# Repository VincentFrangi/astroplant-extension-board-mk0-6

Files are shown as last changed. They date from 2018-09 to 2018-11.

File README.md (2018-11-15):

# Astroplant Extension Board MK0.6

## About This Project

[Interactive BOM](http://htmlpreview.github.io/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)

## Renderings

### Top
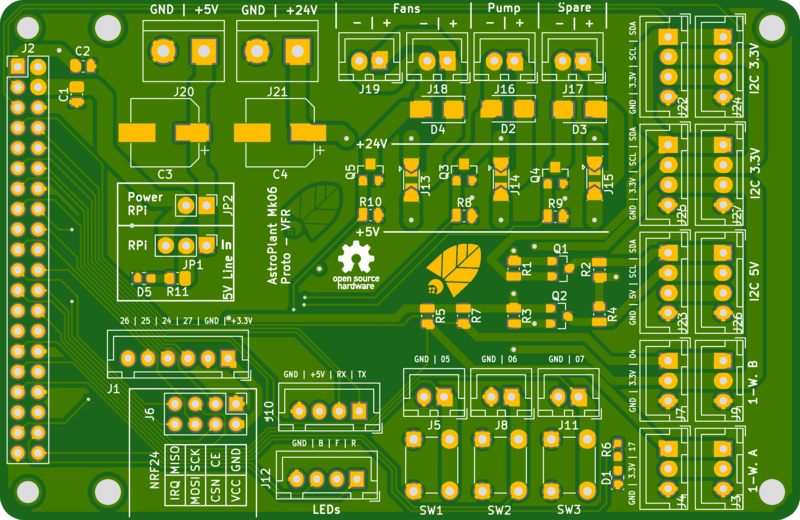
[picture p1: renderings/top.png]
Top Rendering (https://aisler.net/p/DBKSBTQF)


### Bottom
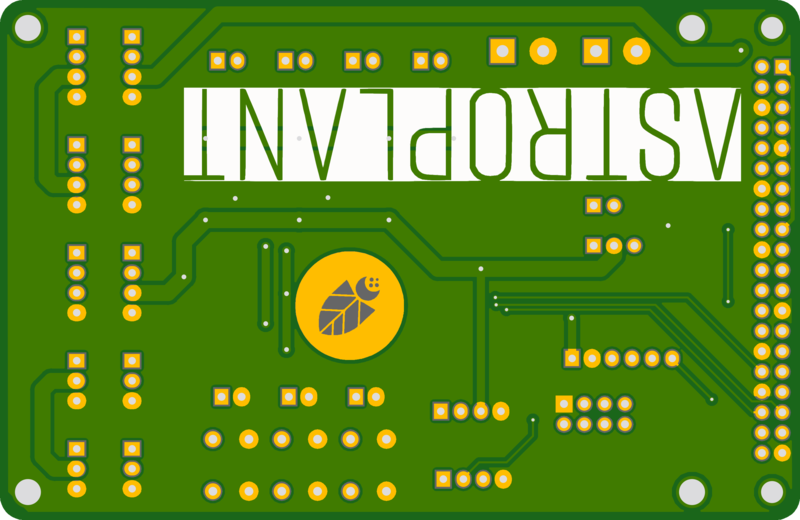
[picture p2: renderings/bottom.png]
Bottom Rendering (https://aisler.net/p/DBKSBTQF)


## BOM

|Count|Component|Details|Datasheet|
|-|-|-|-|
|2x|C1 / C2|CAP CER 0.1UF 25V X7R 0805|[Link](http://datasheets.avx.com/X7RDielectric.pdf)|
|1x|C4|CAP ALUM POLY 470UF 20% 25V SMD|[Link](https://industrial.panasonic.com/cdbs/www-data/pdf/RDD0000/ABA0000C1229.pdf)|
|1x|C3|CAP ALUM POLY 470UF 20% 6.3V SMD|[Link](https://katalog.we-online.de/pbs/datasheet/875115150005.pdf)|
|1x|D1|LED BLUE ESS II SMD|[Link](https://industrial.panasonic.com/content/data/SC/ds/ds4/LNJ937W8CRA_E.pdf)|
|3x|D2 / D3 / D4|DIODE GEN PURP 50V 1A SMA|[Link](http://www.smc-diodes.com/propdf/S1A-S1M%20N0560%20REV.B.pdf)|
|1x|D5|LED AMBER ESS II SMD|[Link](https://industrial.panasonic.com/content/data/SC/ds/ds4/LNJ437W84RA_E.pdf)|
|1x|J1|CONN HEADER XH TOP 6POS 2.5MM|[Link](http://www.jst-mfg.com/product/pdf/eng/eXH.pdf)|
|9x|J10 / J12 / J22 / J23 / J24 / J25 / J26 / J27 / J6|CONN HEADER XH TOP 4POS 2.5MM|[Link](http://www.jst-mfg.com/product/pdf/eng/eXH.pdf)|
|1x|J2|CONN HEADER VERT 40POS 2.54|[Link](http://katalog.we-online.de/em/datasheet/6130xx21121.pdf)|
|2x|J20 / J21|TERM BLOCK 5.08MM VERT 2POS PCB|[Link](http://www.on-shore.com/wp-content/uploads/2015/09/OSTTAXX4163.pdf)|
|7x|J11 / J16 / J17 / J18 / J19 / J5 / J8|CONN HEADER XH TOP 2POS 2.5MM|[Link](http://www.jst-mfg.com/product/pdf/eng/eXH.pdf)|
|4x|J3 / J4 / J7 / J9|CONN HEADER XH TOP 3POS 2.5MM|[Link](http://www.jst-mfg.com/product/pdf/eng/eXH.pdf)|
|1x|JP1|CONN HEADER 3 POS 2.54|[Link](http://katalog.we-online.de/em/datasheet/6130xx11121.pdf)|
|1x|JP2|CONN HEADER 2 POS 2.54|[Link](http://katalog.we-online.de/em/datasheet/6130xx11121.pdf)|
|5x|Q1 / Q2 / Q3 / Q4 / Q5|MOSFET N-CH 30V 5A SOT23|[Link](http://www.infineon.com/dgdl/irlml6344pbf.pdf?fileId=5546d462533600a4015356689c44262c)|
|1x|R11|RES SMD 180 OHM 5% 0.4W 0805|[Link](https://www.rohm.com/datasheet/ESR01MZPF/esr-e)|
|1x|R6|RES SMD 27 OHM 0.5% 1/16W 0603|[Link](http://www.susumu.co.jp/common/pdf/n_catalog_partition05_en.pdf)|
|6x|R1 / R2 / R3 / R4 / R5 / R7|RES SMD 10K OHM 0.5% 1/10W 0805|[Link](http://www.susumu.co.jp/common/pdf/n_catalog_partition05_en.pdf)|
|3x|R10 / R8 / R9|RES SMD 100K OHM 0.1% 1/8W 0805|[Link](http://www.susumu.co.jp/common/pdf/n_catalog_partition01_en.pdf)|
|3x|SW1 / SW2 / SW3|SWITCH TACTILE SPST-NO 0.02A 15V|[Link](https://www3.panasonic.biz/ac/e_download/control/switch/light-touch/catalog/sw_lt_eng_5n.pdf)|

---

This project is managed and available on

AISLER logo (https://aisler.net/p/DBKSBTQF)

You can view it [here](https://aisler.net/p/DBKSBTQF). Start your own Powerful Prototype on [here](https://aisler.net).

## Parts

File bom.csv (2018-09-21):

Count | Component | Details | Datasheet
2x | C1 / C2 | CAP CER 0.1UF 25V X7R 0805 | http://datasheets.avx.com/X7RDielectric.pdf
1x | C4 | CAP ALUM POLY 470UF 20% 25V SMD | https://industrial.panasonic.com/cdbs/www-data/pdf/RDD0000/ABA0000C1229.pdf
1x | C3 | CAP ALUM POLY 470UF 20% 6.3V SMD | https://katalog.we-online.de/pbs/datasheet/875115150005.pdf
1x | D1 | LED BLUE ESS II SMD | https://industrial.panasonic.com/content/data/SC/ds/ds4/LNJ937W8CRA_E.pdf
3x | D2 / D3 / D4 | DIODE GEN PURP 50V 1A SMA | http://www.smc-diodes.com/propdf/S1A-S1M%20N0560%20REV.B.pdf
1x | D5 | LED AMBER ESS II SMD | https://industrial.panasonic.com/content/data/SC/ds/ds4/LNJ437W84RA_E.pdf
1x | J1 | CONN HEADER XH TOP 6POS 2.5MM | http://www.jst-mfg.com/product/pdf/eng/eXH.pdf
9x | J10 / J12 / J22 / J23 / J24 / J25 / J26 / J27 / J6 | CONN HEADER XH TOP 4POS 2.5MM | http://www.jst-mfg.com/product/pdf/eng/eXH.pdf
1x | J2 | CONN HEADER VERT 40POS 2.54 | http://katalog.we-online.de/em/datasheet/6130xx21121.pdf
2x | J20 / J21 | TERM BLOCK 5.08MM VERT 2POS PCB | http://www.on-shore.com/wp-content/uploads/2015/09/OSTTAXX4163.pdf
7x | J11 / J16 / J17 / J18 / J19 / J5 / J8 | CONN HEADER XH TOP 2POS 2.5MM | http://www.jst-mfg.com/product/pdf/eng/eXH.pdf
4x | J3 / J4 / J7 / J9 | CONN HEADER XH TOP 3POS 2.5MM | http://www.jst-mfg.com/product/pdf/eng/eXH.pdf
1x | JP1 | CONN HEADER 3 POS 2.54 | http://katalog.we-online.de/em/datasheet/6130xx11121.pdf
1x | JP2 | CONN HEADER 2 POS 2.54 | http://katalog.we-online.de/em/datasheet/6130xx11121.pdf
5x | Q1 / Q2 / Q3 / Q4 / Q5 | MOSFET N-CH 30V 5A SOT23 | http://www.infineon.com/dgdl/irlml6344pbf.pdf?fileId=5546d462533600a4015356689c44262c
1x | R11 | RES SMD 180 OHM 5% 0.4W 0805 | https://www.rohm.com/datasheet/ESR01MZPF/esr-e
1x | R6 | RES SMD 27 OHM 0.5% 1/16W 0603 | http://www.susumu.co.jp/common/pdf/n_catalog_partition05_en.pdf
6x | R1 / R2 / R3 / R4 / R5 / R7 | RES SMD 10K OHM 0.5% 1/10W 0805 | http://www.susumu.co.jp/common/pdf/n_catalog_partition05_en.pdf
3x | R10 / R8 / R9 | RES SMD 100K OHM 0.1% 1/8W 0805 | http://www.susumu.co.jp/common/pdf/n_catalog_partition01_en.pdf
3x | SW1 / SW2 / SW3 | SWITCH TACTILE SPST-NO 0.02A 15V | https://www3.panasonic.biz/ac/e_download/control/switch/light-touch/catalog/sw_lt_eng_5n.pdf

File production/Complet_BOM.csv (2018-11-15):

Component | Description | Part | References | Value | Footprint | Quantity Per PCB | Datasheet | Digikey Part Number | MPN | SPN1 | URL | Digikey PN | Alternativ
1 | Unpolarized capacitor | C_Small | C1 C2 | 0.1uF | C_0805_2012Metric | 2 | http://catalogs.avx.com/SurfaceMount.pdf | 478-3352-1-ND | 08055C104JAT2A | 478-3352-1-ND | https://www.digikey.com/product-detail/en/avx-corporation/08055C104JAT2A/478-3352-1-ND/930144
2 | Polarised capacitor | CP | C4 | 470uF | CP_Elec_8x11.9 | 1 | http://katalog.we-online.de/pbs/datasheet/875075555002.pdf |  | 875075555002 |  |  | 732-6496-1-ND | EEH-ZK1E471P
3 | Polarised capacitor | CP_Small | C3 | 470uF | CP_Elec_8x6.9 | 1 | http://katalog.we-online.de/pbs/datasheet/875115150005.pdf |  | 875115150005 |  |  | 732-6443-1-ND
4 | LED generic | LED | D5 | LED_Amber | LED_0603_1608Metric | 1 | https://industrial.panasonic.com/content/data/SC/ds/ds4/LNJ437W84RA_E.pdf |  | LNJ437W84RA |  |  | LNJ437W84RACT-ND
5 | LED generic | LED | D1 | LED_Blue | LED_0603_1608Metric | 1 | https://industrial.panasonic.com/content/data/SC/ds/ds4/LNJ937W8CRA_E.pdf |  | LNJ937W8CRA |  |  | LNJ937W8CRACT-ND
6 | Diode, alternativ symbol | D_ALT | D2 D3 D4 | S1A | D_SMA | 3 | https://www.fairchildsemi.com/datasheets/S1/S1A.pdf | S1AFSCT-ND | S1A-13-F |  | https://www.digikey.com/product-detail/en/on-semiconductor/S1A/S1AFSCT-ND/965718
7 | expansion header for Raspberry Pi 2 & 3 | Raspberry_Pi_2_3 | J2 | 2x40 2.5mm Header | Pin_Header_Straight_2x20_Pitch2.54mm | 1 | http://katalog.we-online.de/em/datasheet/6130xx21121.pdf | 732-5310-ND | 61304021121 | 732-5310-ND | https://www.digikey.com/product-detail/en/wurth-electronics-inc/61304021121/732-5310-ND/4846886
8 | Generic screw terminal, single row, 01x02, script generated (kicad-library-utils/schlib/autogen/connector/) | Screw_Terminal_01x02 | J20 J21 | Conn_01x02 | TerminalBlock_bornier-2_P5.08mm | 2 | http://www.on-shore.com/wp-content/uploads/2015/09/OSTTAXX4163.pdf | ED2580-ND | OSTTA024163 |  | https://www.digikey.com/product-detail/en/on-shore-technology-inc/OSTTA024163/ED2580-ND/614529
9 | Generic connector, double row, 02x04, odd/even pin numbering scheme (row 1 odd numbers, row 2 even numbers), script generated (kicad-library-utils/schlib/autogen/connector/) | Conn_02x04_Odd_Even | J6 | Conn_02x04_Odd_Even | Pin_Header_Straight_2x04_Pitch2.54mm | 1
10 | Solder Jumper, 3-pole, open | SolderJumper_3_Open | J13 J14 J15 | GS3 | SolderJumper-3_P2.0mm_Open_TrianglePad1.0x1.5mm | 3
11 | CONN HEADER XH TOP 3POS 2.5MM | JST-XH_3 | J3 J4 J7 J9 | JST-XH_3 | JST_XH_B03B-XH-A_1x03_P2.50mm_Vertical | 4 | http://www.jst-mfg.com/product/pdf/eng/eXH.pdf | 455-2248-ND | B3B-XH-A(LF)(SN) |  | https://www.digikey.com/products/en?keywords=B3B-XH-A(LF)(SN)%20
12 | CONN HEADER XH TOP 4POS 2.5MM | JST-XH_LED_GND | J12 | JST-XH_LED_GND | JST_XH_B04B-XH-A_1x04_P2.50mm_Vertical | 1
13 | CONN HEADER XH TOP 2POS 2.5MM | JST_HX_2 | J5 J8 J11 J16 J17 J18 J19 | JST_HX_2 | JST_XH_B02B-XH-A_1x02_P2.50mm_Vertical | 7 | http://www.jst-mfg.com/product/pdf/eng/eXH.pdf | 455-2247-ND | B2B-XH-A(LF)(SN) |  | https://www.digikey.com/products/en?keywords=%20B2B-XH-A(LF)(SN)%20
14 |  | JST_XH_I2C-Astroplant_VFR-rescue | J22 J23 J24 J25 J26 J27 | JST_XH_I2C | JST_XH_B04B-XH-A_1x04_P2.50mm_Vertical | 6 | http://www.jst-mfg.com/product/pdf/eng/eXH.pdf | 455-2249-ND | B4B-XH-A(LF)(SN) |  | https://www.digikey.com/products/en?keywords=B4B-XH-A(LF)(SN)%20
15 | CONN HEADER XH TOP 6POS 2.5MM | JST_XH_Relays | J1 | JST_XH_Relays | JST_XH_B06B-XH-A_1x06_P2.50mm_Vertical | 1 | http://www.jst-mfg.com/product/pdf/eng/eXH.pdf | 455-2271-ND | B6B-XH-A(LF)(SN) |  | https://www.digikey.com/products/en?keywords=B6B-XH-A(LF)(SN)%20
16 | CONN HEADER XH TOP 4POS 2.5MM | JST_XH_UART | J10 | JST_XH_UART | JST_XH_B04B-XH-A_1x04_P2.50mm_Vertical | 1 | http://www.jst-mfg.com/product/pdf/eng/eXH.pdf | 455-2249-ND | B4B-XH-A(LF)(SN) | 455-2249-ND | https://www.digikey.com/products/en?mpart=B4B-XH-A%28LF%29%28SN%29&v=455
17 | Jumper, 2-pole, closed/bridged | Jumper_2_Bridged | JP2 | Jumper_2_Bridged | PinHeader_1x02_P2.54mm_Vertical | 1 | http://katalog.we-online.de/em/datasheet/6130xx11121.pdf |  | 61300211121 |  |  | 732-5315-ND
18 | Jumper, 3-pole, pins 1+2 closed/bridged | Jumper_3_Bridged12 | JP1 | Jumper_3_Bridged12 | PinHeader_1x03_P2.54mm_Vertical | 1 | http://katalog.we-online.de/em/datasheet/6130xx11121.pdf |  | 61300311121 |  |  | 732-5316-ND
19 | N-Channel 30V 5A (Ta) 1.3W (Ta) Surface Mount Micro3\xe2\x84\xa2/SOT-23 | IRLML6344 | Q1 Q2 Q3 Q4 Q5 | IRLML6344TRPBF | SOT-23 | 5 | https://www.infineon.com/dgdl/irlml6344pbf.pdf?fileId=5546d462533600a4015356689c44262c | IRLML6344TRPBFCT-ND | IRLML6344TRPBF |  | https://www.digikey.com/product-detail/en/infineon-technologies/IRLML6344TRPBF/IRLML6344TRPBFCT-ND/2538168
20 | Resistor | R | R8 R9 R10 | 100K | R_0805_2012Metric | 3 | http://www.yageo.com/documents/recent/PYu-RC_Group_51_RoHS_L_8.pdf | 311-100KCRCT-ND | RC0805FR-07100KL |  | https://www.digikey.com/product-detail/en/yageo/RC0805FR-07100KL/311-100KCRCT-ND/730491 |  | RG2012P-104-B-T5
21 | Resistor, small symbol | R_Small | R1 R2 R3 R4 R5 R7 | 10K | R_0805_2012Metric | 6 | http://www.yageo.com/documents/recent/PYu-RC_Group_51_RoHS_L_8.pdf | 311-10.0KCRCT-ND | RC0805FR-0710KL |  | https://www.digikey.com/product-detail/en/yageo/RC0805FR-0710KL/311-10.0KCRCT-ND/730482 | 311-10.0KCRCT-ND | RR1220P-103-D
22 | Resistor, small symbol | R_Small | R11 | 180 | R_0805_2012Metric | 1 | http://www.rohm.com/web/global/datasheet/ESR01MZPF/esr-e |  | ESR10EZPJ181 |  |  | RHM180KCT-ND
23 | Resistor, small symbol | R_Small | R6 | 27 | R_0603_1608Metric | 1 | http://www.susumu.co.jp/common/pdf/n_catalog_partition05_en.pdf |  | RR0816Q-270-D |  |  | RR08Q27DCT-ND
24 |  | SW_Push-Astroplant_VFR-rescue | SW1 SW2 SW3 | SW_Push | SW_PUSH_6mm | 3 | https://www3.panasonic.biz/ac/e_download/control/switch/light-touch/catalog/sw_lt_eng_5n.pdf | P8009S-ND | EVQ-PAG04M |  | https://www.digikey.com/product-detail/en/panasonic-electronic-components/EVQ-PAG04M/P8009S-ND/91446 | P8009S-ND
Component Groups: | 24
Component Count: | 57
Fitted Components: | 57
Number of PCBs: | 1
Total components: | 57
Schematic Version: | 0.6
Schematic Date: | 2018-05-11
BoM Date: | sam 28 jui 2018 14:15:00 UTC
Schematic Source: | /home/vincent/Documents/AstroPlant_VFR/Project/Electronics/PCB/mk06/Astroplant_VFR.sch
KiCad Version: | Eeschema (5.0.0-rc3-dev)

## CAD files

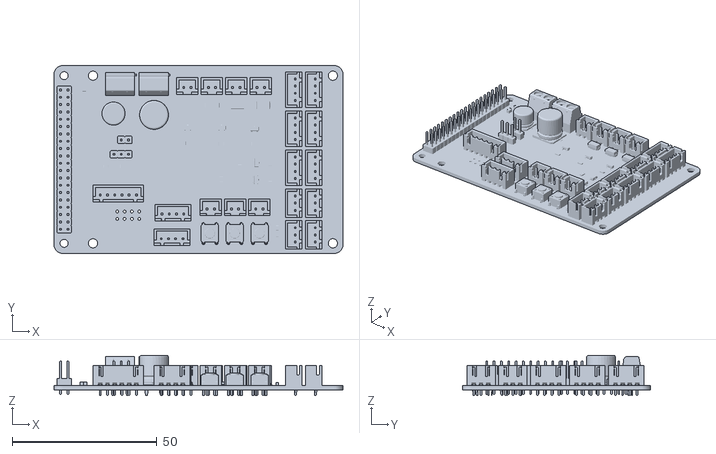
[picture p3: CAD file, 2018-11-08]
3d_model/ExtensionBoardMk06.stl
100.0 x 65.0 x 14.0

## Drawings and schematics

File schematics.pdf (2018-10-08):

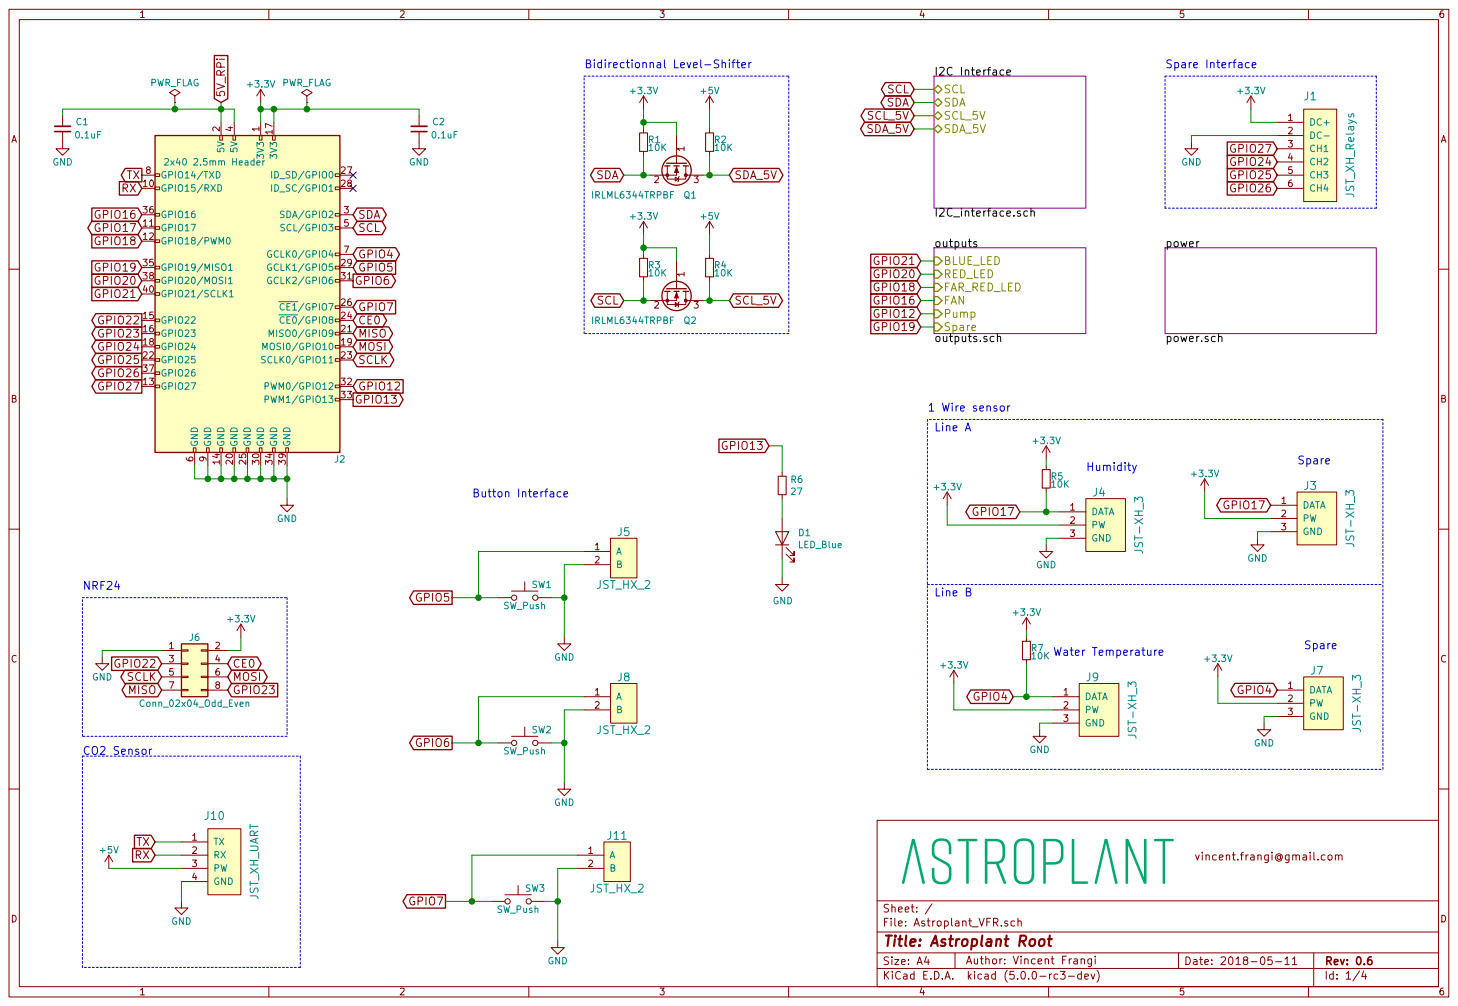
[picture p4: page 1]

Id: 1/4 Title: Astroplant Root

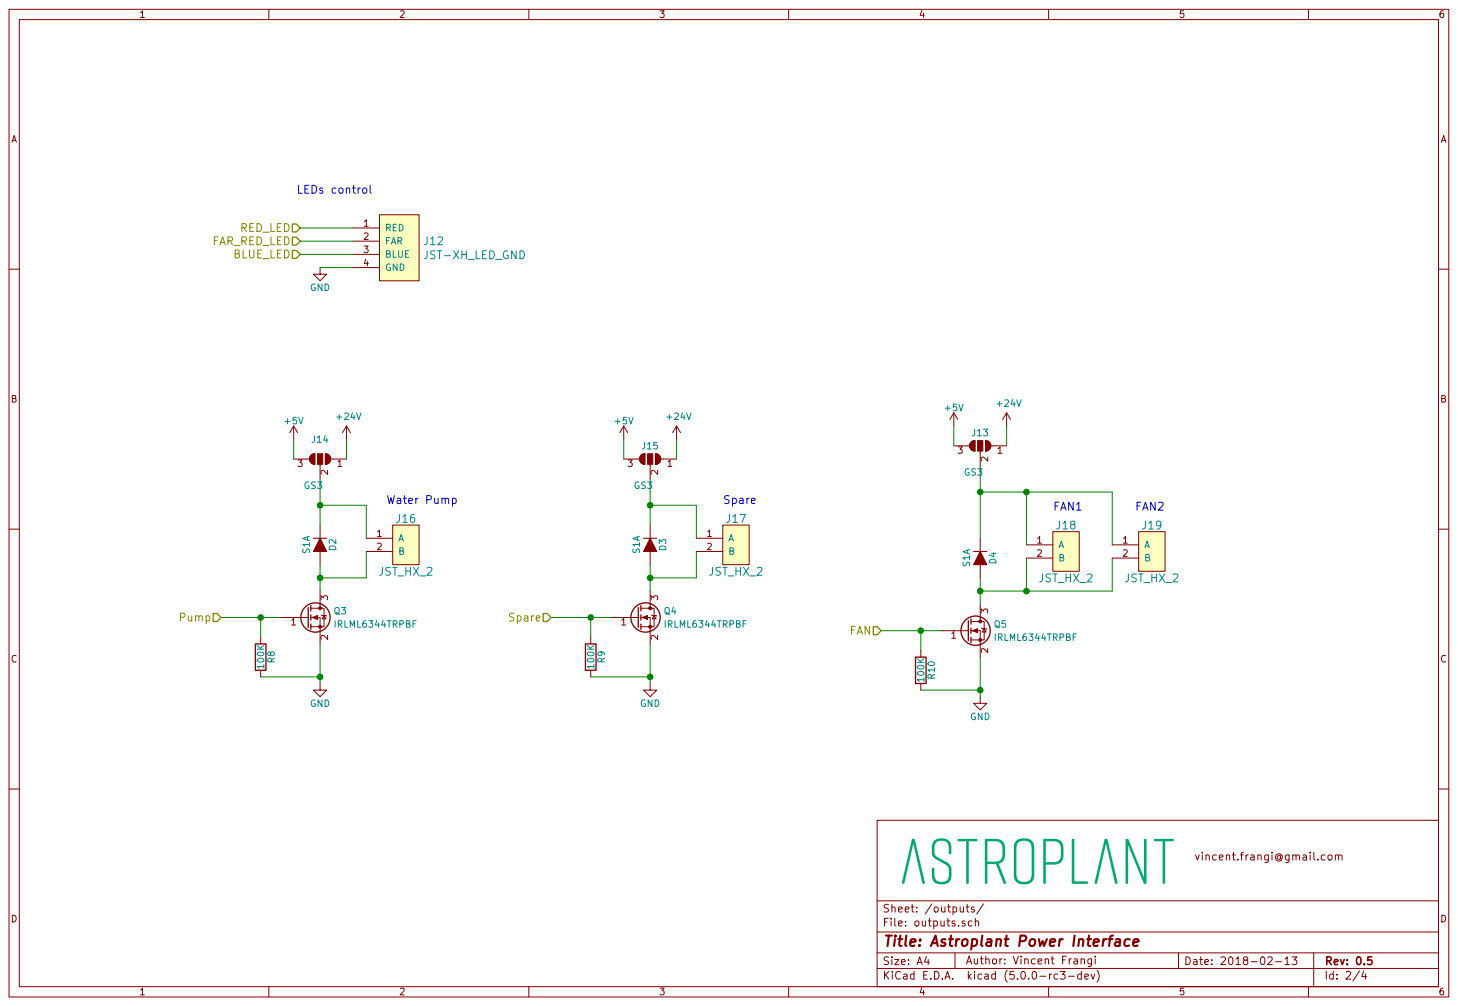
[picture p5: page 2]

vincent.frangi@gmail.com

Sheet: /outputs/
File: outputs.sch
Id: 2/4 Title: Astroplant Power Interface

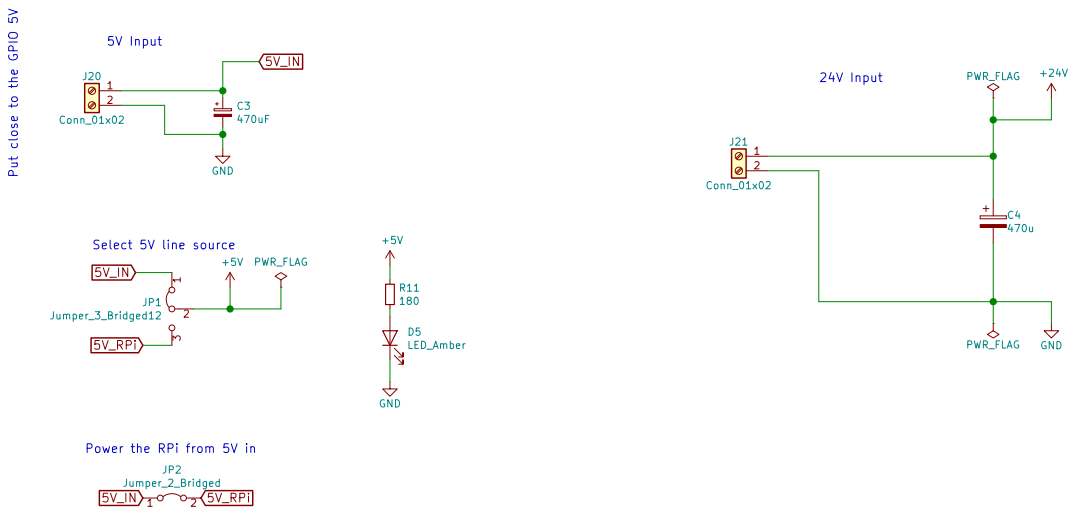
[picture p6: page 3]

vincent.frangi@gmail.com

Sheet: /power/
File: power.sch
Id: 3/4 Title: Power management

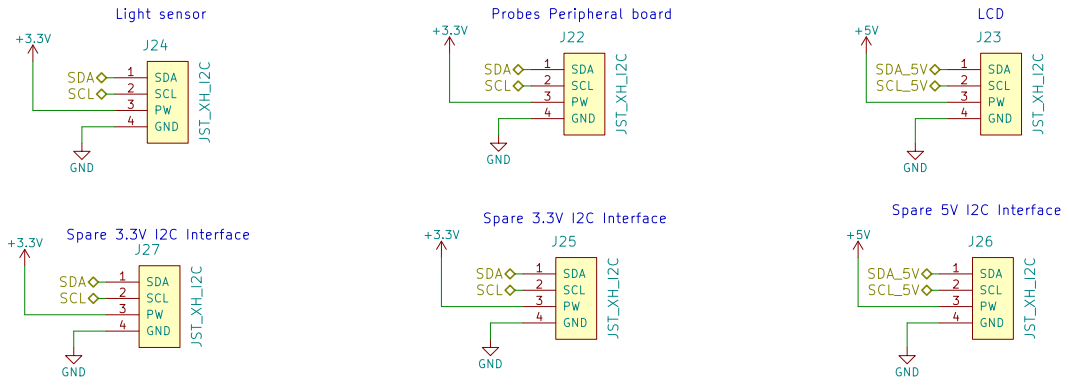
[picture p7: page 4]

Probes Peripheral board GND

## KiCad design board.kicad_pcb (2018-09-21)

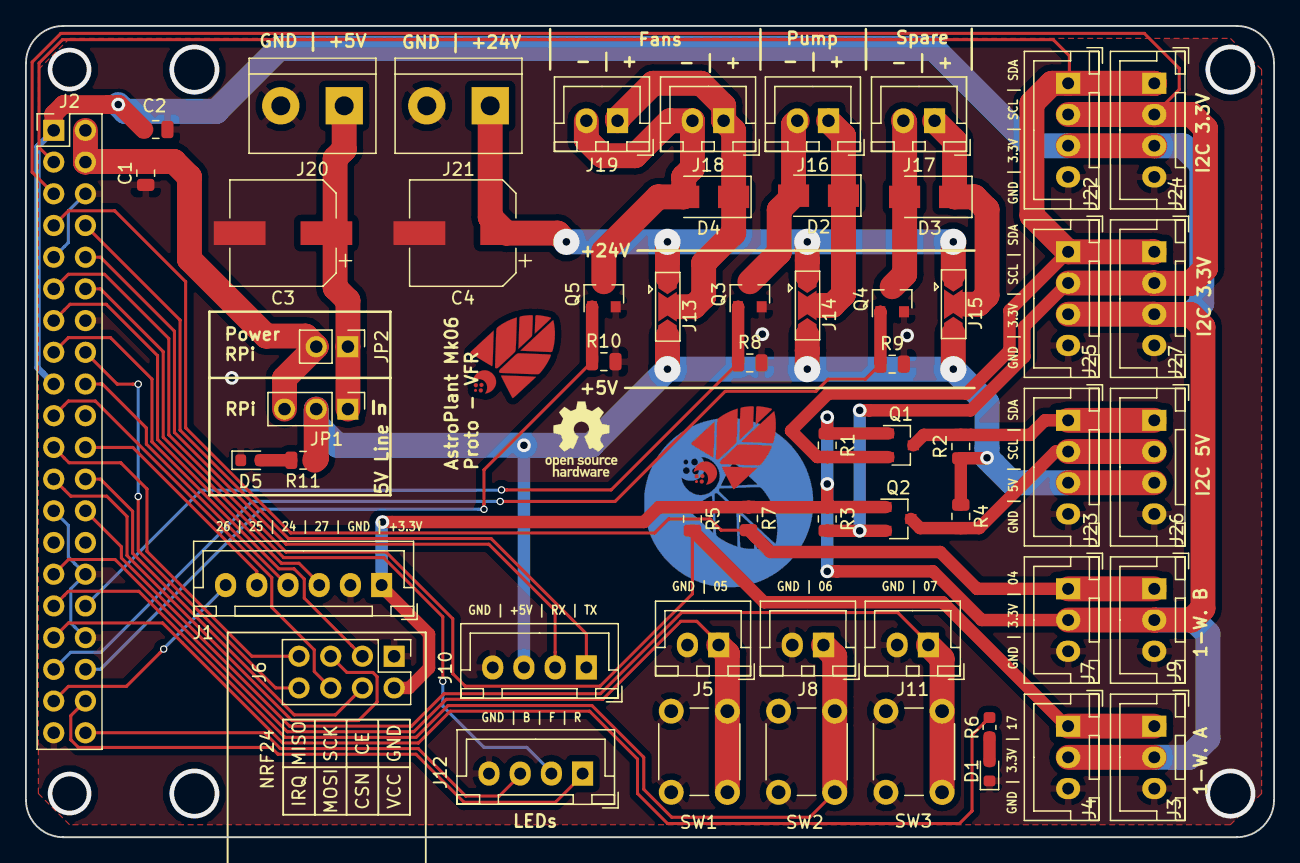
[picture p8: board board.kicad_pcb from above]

Board: 2 copper layers, 100.0 x 65.0 mm, 57 parts (0 on the bottom side), 42 nets.

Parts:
C1, C2: 0.1uF; C_0805_2012Metric
C3: 470uF; CP_Elec_8x6.9
C4: 470u; CP_Elec_8x11.9
D1: LED_Blue; LED_0603_1608Metric
D2, D3, D4: S1A; D_SMA
D5: LED_Amber; LED_0603_1608Metric
J1: JST_XH_Relays; JST_XH_B06B-XH-A_1x06_P2.50mm_Vertical
J2: 2x40 2.5mm Header; Pin_Header_Straight_2x20_Pitch2.54mm
J3, J4, J7, J9: JST-XH_3; JST_XH_B03B-XH-A_1x03_P2.50mm_Vertical
J5, J8, J11, J16, J17, J18, J19: JST_HX_2; JST_XH_B02B-XH-A_1x02_P2.50mm_Vertical
J6: Conn_02x04_Odd_Even; Pin_Header_Straight_2x04_Pitch2.54mm
J10: JST_XH_UART; JST_XH_B04B-XH-A_1x04_P2.50mm_Vertical
J12: JST-XH_LED_GND; JST_XH_B04B-XH-A_1x04_P2.50mm_Vertical
J13, J14, J15: GS3; SolderJumper-3_P2.0mm_Open_TrianglePad1.0x1.5mm
J20, J21: Conn_01x02; TerminalBlock_bornier-2_P5.08mm
J22, J23, J24, J25, J26, J27: JST_XH_I2C; JST_XH_B04B-XH-A_1x04_P2.50mm_Vertical
JP1: Jumper_3_Bridged12; PinHeader_1x03_P2.54mm_Vertical
JP2: Jumper_2_Bridged; PinHeader_1x02_P2.54mm_Vertical
Q1, Q2, Q3, Q4, Q5: IRLML6344TRPBF; SOT-23
R1, R2, R3, R4, R5, R7: 10K; R_0805_2012Metric
R6: 27; R_0603_1608Metric
R8, R9, R10: 100K; R_0805_2012Metric
R11: 180; R_0805_2012Metric
SW1, SW2, SW3: SW_Push; SW_PUSH_6mm

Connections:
5V_IN: C3.1, J20.1, JP1.1, JP2.1
5V_RPi: C1.2, J2.2, J2.4, JP1.3, JP2.2
+3V3: C2.2, J1.1, J2.1, J2.17, J3.2, J4.2, J6.2, J7.2, J9.2, J22.3, J24.3, J25.3, J27.3, Q1.1, Q2.1, R1.1, R3.1, R5.1, R7.1
+5V: J10.3, J13.3, J14.3, J15.3, J23.3, J26.3, JP1.2, R2.1, R4.1, R11.1
+24V: C4.1, J13.1, J14.1, J15.1, J21.1
CE0: J2.24, J6.4
GND: C1.1, C2.1, C3.2, C4.2, D1.1, D5.1, J1.2, J2.6, J2.9, J2.14, J2.20, J2.25, J2.30, J2.34, J2.39, J3.3, J4.3, J5.2, J6.1, J7.3, J8.2, J9.3, J10.4, J11.2, J12.4, J20.2, J21.2, J22.4, J23.4, J24.4, J25.4, J26.4, J27.4, Q3.2, Q4.2, Q5.2, R8.2, R9.2, R10.2, SW1.2, SW2.2, SW3.2
GPIO4: J2.7, J7.1, J9.1, R7.2
GPIO5: J2.29, J5.1, SW1.1
GPIO6: J2.31, J8.1, SW2.1
GPIO7: J2.26, J11.1, SW3.1
GPIO12: J2.32, Q3.1, R8.1
GPIO13: J2.33, R6.1
GPIO16: J2.36, Q5.1, R10.1
GPIO17: J2.11, J3.1, J4.1, R5.2
GPIO18: J2.12, J12.2
GPIO19: J2.35, Q4.1, R9.1
GPIO20: J2.38, J12.1
GPIO21: J2.40, J12.3
GPIO22: J2.15, J6.3
GPIO23: J2.16, J6.8
GPIO24: J1.4, J2.18
GPIO25: J1.5, J2.22
GPIO26: J1.6, J2.37
GPIO27: J1.3, J2.13
MISO: J2.21, J6.7
MOSI: J2.19, J6.6
unnamed: D1.2, R6.2
unnamed: D2.1, J14.2, J16.1
unnamed: D2.2, J16.2, Q3.3
unnamed: D3.1, J15.2, J17.1
unnamed: D3.2, J17.2, Q4.3
unnamed: D4.1, J13.2, J18.1, J19.1
unnamed: D4.2, J18.2, J19.2, Q5.3
unnamed: D5.2, R11.2
RX: J2.10, J10.2
SCL: J2.5, J22.2, J24.2, J25.2, J27.2, Q2.2, R3.2
SCLK: J2.23, J6.5
SCL_5V: J23.2, J26.2, Q2.3, R4.2
SDA: J2.3, J22.1, J24.1, J25.1, J27.1, Q1.2, R1.2
SDA_5V: J23.1, J26.1, Q1.3, R2.2
TX: J2.8, J10.1

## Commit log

2018-09-21 Syncing AISLER project with GitHub repository
    [board.kicad_pcb, bom.csv]
2018-10-08 Addd schematics and production files
    [Complet_BOM.csv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]
2018-11-08 add 3d model
    [ExtensionBoardMk06.stl]
2018-11-15 Add interactiv BOM
2018-11-15 Add link to interactive BOM
2018-11-16 Add front Mask
    [Astroplant_VFR-F.Mask.gbr]
2018-11-19 Add bottom mask
    [Astroplant_VFR-B.Mask.gbr]
